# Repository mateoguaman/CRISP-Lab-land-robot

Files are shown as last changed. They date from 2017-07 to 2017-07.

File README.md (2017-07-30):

# CRISP-Lab-land-robot
## About
Documentation for robot being developed by Mateo Guaman under Professor Usman Khan, Tufts University, 2017
## Goals
The main goal of this project is to develop a four-wheeled land robot that can autonomously detect and navigate to a certain object with specific characteristics (i.e, a certain color or shape) using computer vision.

Other secondary goals of this project are:
- Build an autonomous obstacle avoidance robot without any vision other than an ultrasonic sensor located at the front of the robot.
- Communicate with a Raspberry Pi-controlled drone being developed at the lab through ROS in real time.
- Develop a computer vision algorithm capable of detecting a specific object in real-time and keeping track of the location of said object while navigating to it.

## Challenges
One of the challenges of this project is its low-cost factor, given that the robot is only built with entry-level materials. Another challenge is working the navigation algorithm without the use of motor encoders, just by using data from the ultrasonic sensor on the front and the 9-DOF IMU which includes a 3-axis accelerometer, a 3-axis gyroscope, and a 3-axis magnetometer. However, motor encoders might be incorporated if their use proves to give more precise navigation to the robot.

## Hardware
The robot is a four-wheeled land robot controlled by a Raspberry Pi. The Raspberry Pi controls an Arduino Mega with an Arduino Motor Shield attached to it that sends the power and direction to the DC motors on the wheels, moves the servo motor to the desired angle, and reads the data from the sensors.
### Materials
- 1 Raspberry Pi 3
- 1 Arduino Mega 2560
- 1 Arduino Motor Shield 
- 4 Sparkfun Hobby Gearmotors ROB-13302
- 4 Sparkfun Wheels-65mm ROB-13259
- 1 Parallax PING))) Ultrasonic Distance Sensor
- 1 Servo motor, Hitec HS-422
- 1 Adafruit 9-DOF IMU Breakout - L3GD20H + LSM303, ID:1714
- 1 Breadboard
- 2 24"x12" 1/8" Acrylic Sheets
- 1 LiPo 3S Battery
- 1 Anker PowerCore 13000 Battery Pack
- 1 USB wire for Arduino
- Jumper Wires
### Chassis Design
The chassis for the robot is made of 1/8" acrylic that consists of a 25cm x 15cm rectangle that acts like the base plate of the robot. It also includes two side walls that go through the base plate. The DC motors are attached to these walls below the base plate. Finally, the chassis also includes a structure that holds the servo motor at the front of the robot in place. All of the acrylic parts are connected to each other with M3 screws and nuts.

The chassis was designed using Adobe Illustrator, and the file containing the design can be found on this repo inside the "chassis" folder.

### Circuit
A Fritzing file for the circuit of the robot can be found inside the "files" folder. The Arduino is powered by a LiPo 3S battery connected to the Motor Shield, and the Raspberry Pi should also be connected to power, peripherals, and to the Arduino through a USB cable. Here is an image of the circuit: 
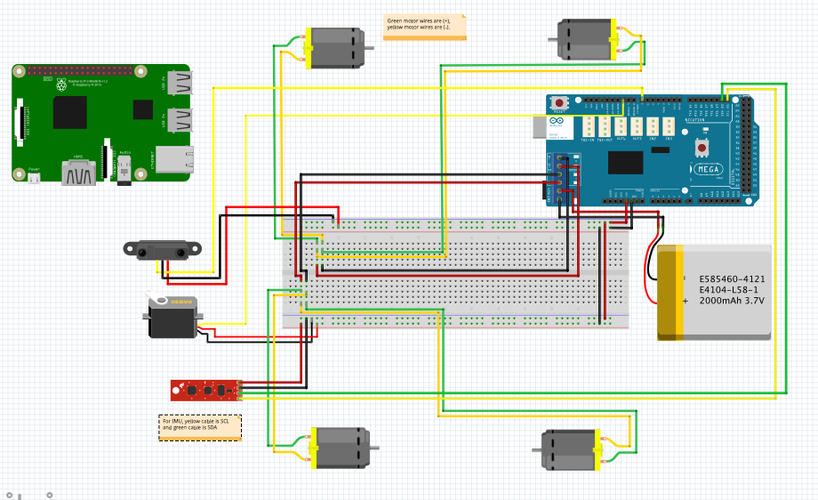
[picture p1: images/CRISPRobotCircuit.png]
Circuit image

### Sensors
- PING))) Ultrasonic Sensor: The PING))) sensor has three pins: +5v, GND, and a signal (SIG) pin. The sensor has a range of approximately 2cm to 30 cm. To initialize the sensor, a short burst has to be sent initially, and then the time it takes for the burst of ultrasound to come back is measured to then calculate the distance, knowing the speed of sound. 
- Adafruit 9 DOF: The Adafruit 9 DOF breakout board includes two different sensors: an L3GD20H Triple-Axis Gyro, and a LSM303 Triple-axis Accelerometer and Magnetometer. These sensors communicate through I2C/SPI. In the case of this robot, the communication is done through I2C. It should be noted that because of the physical layout of the breakout board, the accelerometer and the gyroscope are in opposite directions, which means that the readings from either of these sensors has to be multiplied by -1 to have both of the sensors in the same direction.
## Software
The Raspberry Pi and the Arduino communicate through ROS using the ROSSerial package. 
### Operating System
The Raspberry Pi runs a version of Ubuntu Mate Xenial 16.04 which included ROS Kinetic, downloaded from [german-robot.com](http://www.german-robot.com/2016/05/26/raspberry-pi-sd-card-image/). In order to setup the operating system, the instructions on the page mentioned above and on the official [ROS Kinetic Installation Guide for Ubuntu](http://wiki.ros.org/kinetic/Installation/Ubuntu) were used. 
### Communication
The method of communication between the Raspberry Pi and the Arduino, that reads all the sensors and controls the motors, is through ROS. ROS allows the data to be sent to different nodes as asynchronous messages of different types using publishers and subscribers. Additionally, it also allows data to be sent in a service/client way. One advantage of ROS is that the messages being sent are language agnostic, which means that subscribers and publishers can be coded in either C++ or Python (the two officially supported languages) but the message itself is not in any of these formats. This allows for different nodes to be programmed in either of these two language without modifying the messages sent. ROS provides many packages that can be very useful when dealing with navigation and computer vision, such as tf2 (a transform package) and support for OpenCV. Additionally, it provides different visualization tools such as "rosqt_graph" and "rosqt_plot" which can be used to display the messages being sent through each of the topics and to visualize how the nodes are interconnected. 
### ROS
The Raspberry Pi and the Arduino communicate using ROS through USB using the rosserial package. One feature of ROS is that it includes many preset types of messages that can be used to send messages in a specific format depending on where the data came from or where the data is being sent. For example, the ultrasonic sensor uses the "sensor_msg/Range" type of message to send its readings. 
### Nodes
ROS allows for there to be one main node and multiple secondary nodes that can communicate either to the main node or between secondary nodes. In the case of this robot, at the moment there is only one node on the Arduino which will in the future be one of the secondary nodes. The Arduino can only be one node, which means that all of the data is sent through the same node and that all the messages to control the motors are received on the same node. The goal is to have multiple nodes running on the Raspberry Pi that control different aspects of the motor controller and then send motor speeds to the Arduino node so that the motor moves as desired. For example, on the Raspberry Pi, there would be a node dedicated to processing the data from the IMU to give back an accurate representation of the position and heading of the robot, another node that sends the appropriate motor speeds and directions, and a main node that organizes everything.

TODO: Include visualization of the nodes
### Raspberry Pi
The Raspberry Pi 3 is the brains of the robot. It coordinates all of the nodes in a main node and it will also include additional nodes to do different processes such as navigation, image processing, and sensor data filtering. The Raspberry Pi is powered by a smartphone battery pack so that it can be mounted on the robot. 
#### Setup
As mentioned before, the Raspberry Pi is running Ubuntu Mate Xenial 16.4. The first time that the Raspberry Pi was booted, the filesystem was expanded and SSH was enabled. In the future, the Raspberry Pi will have a Raspberry Pi Camera Module V2.1 attached to it to get the images that will be used to detect objects.
##### ROS
The version of ROS installed on the Raspberry Pi is ROS Kinetic, which was setup following the instructions from the main ROS Tutorials wiki page. 
##### Packages installed
As of now, the packages installed on the Raspberry Pi are rosserial and tf2. Rosserial is mainly used to establish the communication through a serial port with the Arduino, and tf2 will be used to coordinate the transforms of the orientations and rotations of the robot. Additionally, Arduino was installed on the Raspberry Pi following the instructions from the [rosserial tutorials](http://wiki.ros.org/rosserial_arduino/Tutorials/Arduino%20IDE%20Setup). This installs the Arduino IDE so that the programs to the Arduino can be run directly from the IDE, although one goal is to use ROS launch to run the files once the Raspberry Pi is mounted on the robot.
#### Resources used
Some resources used to setup the Raspberry Pi to communicate with the Arduino through ROS are: 
- [Introrobotics](https://www.intorobotics.com/installing-and-setting-up-arduino-with-ros-kinetic-raspberry-pi-3/) to learn how to setup an Arduino with ROS Kinetic on a Raspberry Pi 3

- The official [rosserial wiki](http://wiki.ros.org/rosserial_arduino/Tutorials) to learn more about how rosserial works, how to create publishers and subscribers with the Arduino, examples, and more.
### Nodes on the Raspberry Pi
To come.
#### IMU Filter
#### Motor Driver
#### Image Processing
#### Main Node

### Arduino
The Arduino acts like an interface between the sensors and motors and the main processing unit of the robot, which in this case is the Raspberry Pi. The Arduino used in this robot is an Arduino Mega because of its increased processing power, memory, and number of pins available compared to an Arduino Uno. An Arduino Motor Shield controls the DC motors for the wheels, because of its ease of use and because it allows more power to be sent to the motors. Again, the Raspberry Pi and the Arduino communicate using the rosserial package on the Raspberry Pi.

To run files and receive data from the Arduino, a few steps need to be completed first:
1. On the terminal window, run ```roscore```
2. Upload the program to the Arduino from the Arduino IDE (the first line of this file should be ```#include <ros.h>```), making sure the right Arduino board and serial port are selected on the "Tools" window.
3. On another terminal window, run ```rosrun rosserial_python serial_node.py _port:=/dev/ttyACM0 _baud:=9600``` changing ```ttyACM0``` and ```9600``` depending on the values needed, which initiates the serial communication with the Arduino.
4. After doing these, the terminal should indicate which subscribers/publishers exist, and these can be accessed using ROS tools such as ```rostopic echo {}``` with the brackets being replaced by the topic and message you want to see.
#### Arduino Node
The Arduino can only be used to run one ROS node, so this node is in charge of handling the reading of the sensors, sending them to the Raspberry Pi, and receiving commands for the motors. The code for this node can be found in this repo under the name of robotNode.ino.

##### Messages
The program includes different types of messages that are used to communicate the information to the sensors in a more organized manner. There are three different types of messages used in this program: standard messages, geometry messages, and sensor messages. 

The standard messages used in this program are:
- Float64: used to receive the power that should be given to the motors (0-255 to move forward or -255-0 to move backward). Floats are used in this case because the power sent to the motors can be either positive or negative to indicate in which direction the motors should rotate.
- UInt16: used to receive the angle that the servo motor should move to. The servo motor can only move between 0-180 degrees, which means that the unsigned integer suffices for this purpose.  

The geometry messages used in this program are:
- Vector3: This message is used to represent a three dimensional vector of float64 numbers to represent the x, y, and z axes. This message is used in this code to create 3D linear acceleration (from accelerometer), 3D angular velocity (from gyroscope), and 3D magnetic field (from magnetometer) vectors. Additionally, this type of message is also being used to send the roll, pitch, and yaw (or heading) computed on the Arduino by one of Adafruit's libraries used, described in another section of this README. 
- Vector3Stamped: This type of message is very similar to the Vector3 message, but it includes a header for the message (which is actually another ROS standard message) that includes a time stamp of the vector and a frame ID. This message is used in this program to send the rpy (roll, pitch, and yaw) vector described above to the Raspberry Pi with a timestamp so that it can be known when this message was sent. 

The sensor messages used in this program are: 
- Range: This message is used to send the range data measured by the PING))) Ultrasonic Sensor as a float32 data type in meters. Additionally, it sends information about the sensor and a header message. The information about the sensor that it sends include the radiation type that the sensor uses to detect distance (Infrared or Ultrasound), the field-of-view of the sensor as an arc in radians, and the minimum and maximum ranges of the sensor. The header message, as explained above, sends a frame ID for the sensor and a timestamp of when the reading happened.
- IMU: This message is used to send inertial information about the robot. It has the ability to send three geometry messages: an orientation quaternion, an angular velocity Vector3. and a linear acceleration Vector3. Additionally, it allows to send a 9-float64 array for each of the mentioned measurements' covariances. Finally, it also allows a header file, again, with a timestamp and a frame ID, to be sent alongside the sensor readings. In the case of this program, only the linear acceleration and the angular velocity vectors are sent, as well as the header file. The data being sent from this message allows the Raspberry Pi to know the orientation of the robot at any given time. The Adafruit 9-DOF IMU sensor also includes a magnetometer, but this type of message does not support data from this sensor to be sent. 
- MagneticField: In order to have a magnetic field reading from the IMU to be able to calculate a more accurate orientation, the MagneticField message is used to send a 3D vector of the magnetic field readings in all three axes as a Vector3 and a 9-float64 array of the magnetic field covariance. Additionally, this message also includes a header file, so it sends a timestamp and a frame ID alongside the sensor readings.

##### Using the IMU
The IMU uses four different libraries created by Adafruit to collect the data needed for the robot. It uses the Adafruit Sensor llibrary which incorporates a framework that abstracts how the data is recollected and makes it easy to use different Adafruit sensors in a very similar way. This program also uses the libraries for each of the two sensors in the IMU, the LSM303 Accelerometer and Magnetometer and the L3GD20 Gyroscope. These libraries have very useful functions that make it easy to get the sensor readings in each of the axes for each of the sensors. Finally, the Adafruit 9DOF function is used because it provides functions that calculate the roll, pitch, and yaw automatically. 

Each one of these sensors has a data structure that is used to later get the data from the sensors using the Adafruit Sensors library, which uses sensor events to get the data. The whole 9-DOF unit also has a data structure that can be used to hold the RPY data. The three sensors, accelerometer, magnetometer and gyroscope, need to be initialized with the function ```sensor.begin()```, which handles the communication over I2C (using the Arduino's Wire.h library) for each of the sensors and returns a boolean that tells if the sensor communication was initialized correctly or not. 

Later in the code, in the loop() function, each one of the sensors is given a variable of type "sensors_event_t" that is used as a parameter to the Adafruit Sensors Library's function ```getEvent()``` to get the data for the three axes of each sensor's readings. There is also an orientation variable of type "sensors_vec_t" that is used by the Adafruit 9-DOF Library to generate the RPY of the IMU. After getting all these readings, they can all be asigned to their respective Vector3 that will then be sent inside either the IMU message, the MagneticField message, or the RPY message.

##### DC Motors
The Arduino Motor Shield has two motor channels, A and B. The A channel controls the left-side motors and the B channel controls the motors on the right side of the robot. The two motors on each side are connected in parallel to the two pins for each of the channels. However, because the motors on the front and back on each side are facing each other, one of the motors needs to be connected to opposite charges. This means that one motor's positive and negative pins are connected to the positive and negative pins on the motor shield, but the other motor's positive and negative pins are connected to the negative and positive pins on the motor shield respectively. 

Each of the motor channels on the Motor Shield has pins on the Arduino that control the PWM, direction, and breaking of the motors connected to each channel. This means that sending commands to the motors is as easy as writing ```HIGH``` or ```LOW``` with the Arduino's ```digitalWrite()``` function or values from 0-255 with the ```analogWrite()``` function for PWM. Each of these pins, which are specified on the documentation for the Arduino Motor Shield and in the first lines of the robotNode.ino program in this repo, has to be declared inside the ```setup()``` function as an OUTPUT pin using the ```pinMode()``` Arduino function. Each one of this channels has a callback function that runs when a float64 is sent to the motor subscribers, which will be described later in more detail. These callback functions determine if the float is positive, negative, or zero and write the approriate direction and PWM to the respective channels. 

Inside the ```setup()``` function, the direction of the motors is set to forward and their speeds are set to 0.
##### Servo
The code for the servo motor uses the Arduino's Servo.h library. The use of this library is really simple, as it only requires one variable of the Servo data structure to be declared and later, inside the ```setup()``` function, for this variable to be attached to a pin number using the member function ```servo.attach(pinNumber)```. To move the servo motor to a certain position, it is as simple as using the function ```servo.write(angle)```. The servo motor is connected to a ROS subscriber which runs a callback function once a message is sent to a topic. This callback function receives a UInt16 which determines the angle (0-180) to which the servo should move, and it simply writes the servo motor to this number using the function described above.
##### Ultrasound
As mentioned above in the description for the PING))) sensor, this sensor has one pin that is used to send and receive signals. It has to be initialized by sending a short 10ms burst and then changing to receiving mode (INPUT) and records the time it takes for the signal to come back. This time is then multiplied by a constant to determine the distance, knowing what the speed of sound is. In the case of this program, that constant is 1/58, which gives back the distance in cm. All of this code is part of a function that is called inside the ```loop()``` function every 50ms, as that is the time it takes for the sensor to reset and be able to send another burst.  
##### ROS
Although it would be relatively easy to send information to/from the Arduino using normal serial communication, it is more convenient to use ROS for communication as it allows different nodes to communicate each other in a direct, standardized way, and it gives access to all the advantages of using ROS and its packages. Libraries for ROS, ROS/time, and all the ROS messages need to be included in the code. A ROS node handle needs to be declared as a global variable of type ```ros::NodeHandle```. All of the sensor messages variables are also declared as global variables in this program with their respective data type. All of the subscribers and publisher are also declared as global variables and as specified on the official beginner ROS tutorials. 

Inside of the ```setup()``` function, the ROS node has to be initialized calling th ```init()``` on the ROS handle, the publishers need to be published using the ```advertise``` function and the subscribers need to be set to receive messages using the ```subscribe``` function as used in the code. 

Inside the ```loop()``` function, the timestamps for the sensor readings can be set using the function ```nh.now()``` that returns the time when that line of code was run, nh being the node handle. The publishers can be published by calling the ```publish``` function on the publisher variables. At the end of the loop, the function ```nh.spinOnce()``` should be called in order for callbacks to be processed correctly.

## Images
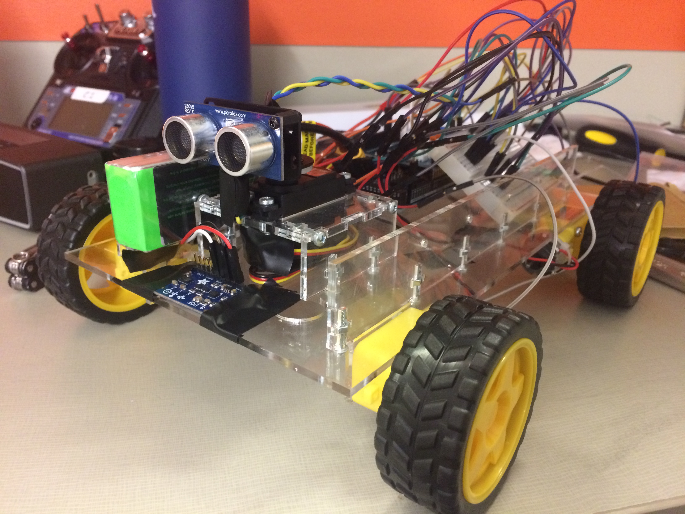
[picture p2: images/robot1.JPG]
Picture of Robot

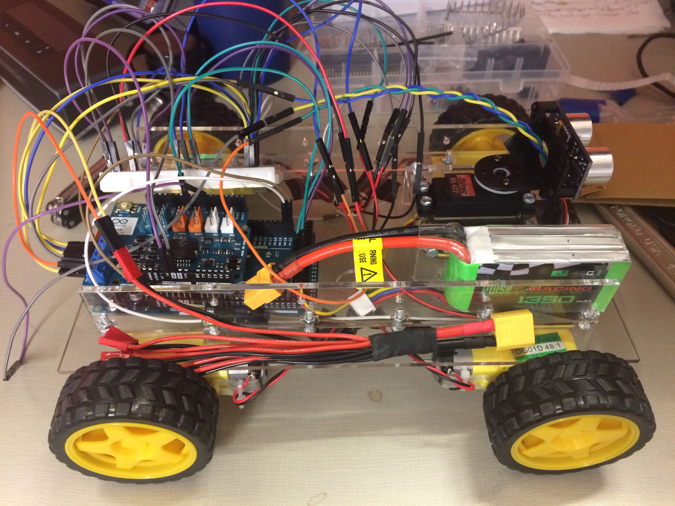
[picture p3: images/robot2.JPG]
Picture of Robot


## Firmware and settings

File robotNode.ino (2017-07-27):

#include <ros.h>
#include <ros/time.h>
#include <Wire.h>
#include <std_msgs/UInt16.h>
#include <std_msgs/Float64.h>
#include <geometry_msgs/Vector3.h>
#include <geometry_msgs/Vector3Stamped.h>
#include <sensor_msgs/MagneticField.h>
#include <sensor_msgs/Imu.h>
#include <sensor_msgs/Range.h>
#include <Servo.h>
#include <Adafruit_Sensor.h>
#include <Adafruit_LSM303_U.h>
#include <Adafruit_L3GD20_U.h>
#include <Adafruit_9DOF.h>

#define A_DIR 12
#define A_BRK 8
#define A_PWM 3
#define B_DIR 13
#define B_BRK 9
#define B_PWM 11

ros::NodeHandle nh;

Servo servo;

int commandL = 0;
int commandR = 0;

sensor_msgs::Range range_msg;
sensor_msgs::MagneticField mag_msg;
sensor_msgs::Imu imu_msg;
geometry_msgs::Vector3Stamped rpy_msg;
geometry_msgs::Vector3 accel_vec;
geometry_msgs::Vector3 gyro_vec;
geometry_msgs::Vector3 mag_vec;
geometry_msgs::Vector3 rpy_vec;

char frameidUS[] = "/ultrasound";
char frameidMag[] = "/magnetometer";
char frameidImu[] = "/imu";
char frameidRpy[] = "/rpy";

Adafruit_9DOF dof = Adafruit_9DOF();
Adafruit_LSM303_Accel_Unified accel = Adafruit_LSM303_Accel_Unified(30301);
Adafruit_LSM303_Mag_Unified mag = Adafruit_LSM303_Mag_Unified(30302);
Adafruit_L3GD20_Unified gyro = Adafruit_L3GD20_Unified(20);

long range_time;
long duration;

float roll;
float pitch;
float heading;
float accelX;
float accelY;
float accelZ;
float gyroX;
float gyroY;
float gyroZ;
float magX;
float magY;
float magZ;

void initSensors()
{

    accel.enableAutoRange(true);
    if(!accel.begin())
    {
        /* There was a problem detecting the LSM303 ... check your connections */
        Serial.println(F("Ooops, no LSM303 detected ... Check your wiring!"));
        while(1);
    }

    mag.enableAutoRange(true);
    if(!mag.begin())
    {
        /* There was a problem detecting the LSM303 ... check your connections */
        Serial.println("Ooops, no LSM303 detected ... Check your wiring!");
        while(1);
    }

    gyro.enableAutoRange(true);
    if(!gyro.begin())
    {
        /* There was a problem detecting the L3GD20 ... check your connections */
        Serial.println("Ooops, no L3GD20 detected ... Check your wiring!");
        while(1);
    }
}

void servo_cb(const std_msgs::UInt16& cmd_msg)
{
    servo.write(cmd_msg.data);
}

void motorsCbL(const std_msgs::Float64& msg)
{
    commandL = msg.data;
    
    if (commandL == 0.0)
    {
        digitalWrite(A_DIR, LOW);
        analogWrite(A_PWM, commandL);
    }
    else if (commandL < 0)
    {
        //Forward: Direction = LOW; Backward: Direction = HIGH
        digitalWrite(A_DIR, HIGH);
        analogWrite(A_PWM, commandL);
    }
    else
    {
        digitalWrite(A_DIR, LOW);
        analogWrite(A_PWM, commandL);
    }
}

void motorsCbR(const std_msgs::Float64& msg)
{
    commandR = msg.data;
    
    if (commandR == 0.0)
    {
        digitalWrite(B_DIR, LOW);
        analogWrite(B_PWM, commandR);
    }
    else if (commandR < 0)
    {
        //Forward: Direction = LOW; Backward: Direction = HIGH
        digitalWrite(B_DIR, HIGH);
        analogWrite(B_PWM, commandR);
    }
    else
    {
        digitalWrite(B_DIR, LOW);
        analogWrite(B_PWM, commandR);
    }
}

float getRange_Ultrasound(int pin_num)
{
    pinMode(pin_num, OUTPUT);
    digitalWrite(pin_num, LOW);
    delayMicroseconds(2);
    digitalWrite(pin_num, HIGH);
    delayMicroseconds(10);
    digitalWrite(pin_num, LOW);
    
    pinMode(pin_num, INPUT);
    duration = pulseIn(pin_num, HIGH);
    
    return duration/58;
}

ros::Subscriber<std_msgs::UInt16> sub_servo("servo", servo_cb);
ros::Subscriber<std_msgs::Float64> sub_left("leftMotors", &motorsCbL);
ros::Subscriber<std_msgs::Float64> sub_right("rightMotors", &motorsCbR);
ros::Publisher pub_mag("magnetometer", &mag_msg);
ros::Publisher pub_imu("imu", &imu_msg);
ros::Publisher pub_rpy("rpy", &rpy_msg);
ros::Publisher pub_range("ultrasound", &range_msg);

void setup()
{
    //Serial.begin(57600);
    pinMode(A_DIR, OUTPUT);
    pinMode(A_BRK, OUTPUT);
    pinMode(A_PWM, OUTPUT);
    pinMode(B_DIR, OUTPUT);
    pinMode(B_BRK, OUTPUT);
    pinMode(B_PWM, OUTPUT);
    
    nh.initNode();
    nh.advertise(pub_range);
    nh.advertise(pub_mag);
    nh.advertise(pub_imu);
    nh.advertise(pub_rpy);
    nh.subscribe(sub_servo);
    nh.subscribe(sub_left);
    nh.subscribe(sub_right);
    
    initSensors();
    servo.attach(10);
    
    digitalWrite(A_DIR, LOW);
    analogWrite(A_PWM, 0);
    digitalWrite(B_DIR, LOW);
    analogWrite(B_PWM, 0);
    
    range_msg.header.frame_id = frameidUS;
    mag_msg.header.frame_id = frameidMag;
    imu_msg.header.frame_id = frameidImu;
    rpy_msg.header.frame_id = frameidRpy;
    
    range_msg.radiation_type = sensor_msgs::Range::ULTRASOUND;
    range_msg.field_of_view = 0.1;
    range_msg.min_range = 0.02;
    range_msg.max_range = 3.0;
}

void loop()
{
    sensors_event_t accel_event;
    sensors_event_t mag_event;
    sensors_event_t gyro_event;
    sensors_vec_t orientation;
    
    accel.getEvent(&accel_event);
    accelX = accel_event.acceleration.x;
    accelY = accel_event.acceleration.y;
    accelZ = accel_event.acceleration.z;
    
    gyro.getEvent(&gyro_event);
    gyroX = gyro_event.gyro.x;
    gyroY = gyro_event.gyro.y;
    gyroZ = gyro_event.gyro.z;
    
    mag.getEvent(&mag_event);
    magX = mag_event.magnetic.x;
    magY = mag_event.magnetic.y;
    magZ = mag_event.magnetic.z;
    
    if (dof.accelGetOrientation(&accel_event, &orientation))
    {
        roll = orientation.roll;
        pitch = orientation.pitch;
    }
    
    if (dof.magGetOrientation(SENSOR_AXIS_Z, &mag_event, &orientation))
    {
        heading = orientation.heading;
    }
    
    accel_vec.x = accelX;
    accel_vec.y = accelY;
    accel_vec.z = accelZ;
    
    gyro_vec.x = gyroX;
    gyro_vec.y = gyroY;
    gyro_vec.z = gyroZ;
    
    mag_vec.x = magX;
    mag_vec.y = magY;
    mag_vec.z = magZ;
    
    rpy_vec.x = roll;
    rpy_vec.y = pitch;
    rpy_vec.z = heading;
    
    imu_msg.angular_velocity = gyro_vec;
    imu_msg.linear_acceleration = accel_vec;
    imu_msg.header.stamp = nh.now();
    mag_msg.header.stamp = nh.now();
    rpy_msg.header.stamp = nh.now();
    mag_msg.magnetic_field = mag_vec;
    rpy_msg.vector = rpy_vec;
    
    if ((millis()-range_time) > 50)
    {
        range_msg.range = getRange_Ultrasound(7);
        range_msg.header.stamp = nh.now();
        pub_range.publish(&range_msg);
        range_time = millis();
    }
    pub_mag.publish(&mag_msg);
    pub_imu.publish(&imu_msg);
    pub_rpy.publish(&rpy_msg);
    
    nh.spinOnce();    
}

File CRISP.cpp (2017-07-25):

#include <Wire.h>
#include <Adafruit_Sensor.h>
#include <Adafruit_LSM303_U.h>
#include <Adafruit_L3GD20_U.h>
#include <Adafruit_9DOF.h>
#include <Servo.h>

//=================================================================
//                              SERVO
//=================================================================
  
Servo myservo; 
//Set initial position to be 90º
int pos = 90;

//=================================================================
//                              PING)))
//=================================================================
   
//Pin for signal pin in Parallax PING)))
const int pingPin = 7;

//=================================================================
//                              Motors
//=================================================================

//PWM speeds for DC motors
const int zero = 0, fullSpeed = 255, halfSpeed = 128, quarterSpeed = 64, threeQuarterSpeed = 191; 

int driveSpeed = zero;
int min_distance = 20;
bool keepScanning = true;

//=================================================================
//                              IMU
//=================================================================

Adafruit_9DOF dof = Adafruit_9DOF();
Adafruit_LSM303_Accel_Unified accel = Adafruit_LSM303_Accel_Unified(30301);
Adafruit_LSM303_Mag_Unified   mag   = Adafruit_LSM303_Mag_Unified(30302);
Adafruit_L3GD20_Unified gyro = Adafruit_L3GD20_Unified(20);
float seaLevelPressure = SENSORS_PRESSURE_SEALEVELHPA;

float roll;
float pitch;
float heading;
float accelX;
float accelY;
float accelZ; 
float gyroX;
float gyroY;
float gyroZ;

//=================================================================
//                              Extra
//=================================================================

// establish variables for duration of the ping,
// and the distance result in inches and centimeters:
long duration, inches, cm;

void initSensors()
{

    accel.enableAutoRange(true);
    if(!accel.begin())
    {
        /* There was a problem detecting the LSM303 ... check your connections */
        Serial.println(F("Ooops, no LSM303 detected ... Check your wiring!"));
        while(1);
    }

    mag.enableAutoRange(true);
    if(!mag.begin())
    {
        /* There was a problem detecting the LSM303 ... check your connections */
        Serial.println("Ooops, no LSM303 detected ... Check your wiring!");
        while(1);
    }

    gyro.enableAutoRange(true);
    if(!gyro.begin())
    {
        /* There was a problem detecting the L3GD20 ... check your connections */
        Serial.println("Ooops, no L3GD20 detected ... Check your wiring!");
        while(1);
    }
}

void setup() 
{
    Serial.begin(9600);
    myservo.attach(10);
    pinMode(8,OUTPUT);       //Channel A Brake Pin Initialize
    pinMode(9,OUTPUT);       //Channel B Brake Pin Initialize 
    pinMode(12,OUTPUT);      //Channel A Direction Pin Initialize
    pinMode(13,OUTPUT);      //Channel B Direction Pin Initialize

    myservo.write(90);

    initSensors();    
}

void loop() 
{

    Serial.println("===============================================");

//=================================================================
//                              SERVO
//=================================================================
    
    myservo.write(90);
    Serial.print("The position of the Servo is: ");
    Serial.println(myservo.read());
    
//=================================================================
//                              PING)))
//=================================================================
    
    duration = calculateDuration();
    cm = microsecondsToCentimeters(duration);
    Serial.print("The PING))) sensor detects object at: ");
    Serial.println(cm);

//=================================================================
//                              Motors
//=================================================================

    forward(0.1, driveSpeed);
    Serial.print("The motors are running at a speed of: ");
    Serial.println(driveSpeed);
     
//=================================================================
//                              IMU
//=================================================================

    sensors_event_t accel_event;
    sensors_event_t mag_event;
    sensors_event_t gyro_event;
    sensors_vec_t   orientation;

    accel.getEvent(&accel_event);

    accelX = accel_event.acceleration.x;
    accelY = accel_event.acceleration.y;
    accelZ = accel_event.acceleration.z;

    Serial.print("The accelerometer is reading a X, Y, Z acceleration of: ");
    Serial.print(accelX);
    Serial.print(", ");
    Serial.print(accelY);
    Serial.print(", ");
    Serial.println(accelZ);

   if (dof.accelGetOrientation(&accel_event, &orientation))
    {
        roll = orientation.roll;
        pitch = orientation.pitch;
        Serial.print("The accelerometer is reading a roll of: ");
        Serial.println(roll);
        Serial.print("The acceloremeter is reading a pitch of: ");
        Serial.println(pitch);
    }

    mag.getEvent(&mag_event);
    magX = mag_event.magnetic.x;
    magY = mag_event.magnetic.y;
    magZ = mag_event.magnetic.z;
    if (dof.magGetOrientation(SENSOR_AXIS_Z, &mag_event, &orientation))
    {
        heading = orientation.heading;
        Serial.print("The magnetometer (compass) is reading a heading of: ");
        Serial.println(heading);
    }

    gyro.getEvent(&gyro_event);
    gyroX = gyro_event.gyro.x;
    gyroY = gyro_event.gyro.y;
    gyroZ = gyro_event.gyro.z;

    Serial.print("The gyro is reading a X, Y, Z acceleration of: ");
    Serial.print(gyroX);
    Serial.print(", ");
    Serial.print(gyroY);
    Serial.print(", ");
    Serial.println(gyroZ);

//=================================================================
    Serial.println("===============================================");
    delay(1000);
  
}

//=================================================================
//                              Motors
//=================================================================

long microsecondsToInches(long microseconds) 
{
    // According to Parallax's datasheet for the PING))), there are
    // 73.746 microseconds per inch (i.e. sound travels at 1130 feet per
    // second).  This gives the distance travelled by the ping, outbound
    // and return, so we divide by 2 to get the distance of the obstacle.
    // See: http://www.parallax.com/dl/docs/prod/acc/28015-PING-v1.3.pdf
    return microseconds / 74 / 2;
}

long microsecondsToCentimeters(long microseconds) 
{
    // The speed of sound is 340 m/s or 29 microseconds per centimeter.
    // The ping travels out and back, so to find the distance of the
    // object we take half of the distance travelled.
    return microseconds / 29 / 2;
}
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

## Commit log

2017-07-15 All sensors connected and print current status to serial
2017-07-20 Publisher for PING))) sensor
2017-07-20 Servo subscriber
2017-07-21 New IMU guide link added
2017-07-22 Reading 3d vectors of acceleration and gyroscope only
2017-07-22 Added information about sensors in the IMU
2017-07-22 added resources on IMUs and quaternions
2017-07-25 removed IR sensors and included magnetometer readings
2017-07-25 Publisher for imu and magnetometer sensors
2017-07-27 Contains publishers/subscriber for servo, ultrasound ranger, and IMU, including RPY
2017-07-27 DC Motors' subscriber
2017-07-27 Complete publishers/subscribers for all sensors/motors on the robot
2017-07-28 Added chassis Illustrator file
2017-07-28 Added supporting files
    [Robot.fzz]
